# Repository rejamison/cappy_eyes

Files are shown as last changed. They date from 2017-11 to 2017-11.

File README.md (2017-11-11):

# cappy_eyes

Fun little project to create a moving pair of Cappy eyes for a hat.

Cappy Eyes

## 3D Printing

|Part|Count|Material|Print Time|Supports|
|---|---|---|---|---|
|[cappy_eyes.stl](cad/cappy_eyes.stl)|x1|40g|5 hours|No|
|[cappy_eyes_pupil.stl](cad/cappy_eyes_pupil.stl)|x2|2g|1 hour|No|
|[cappy_eyes_pupils_rail.stl](cad/cappy_eyes_pupils_rail.stl)|x1|1g|10 mins|No|
|[cappy_eyes_mount.stl](cad/cappy_eyes_mount.stl)|x1|2g|20 mins|Yes|
|**Total**| |**45g**|**6 hours**|

* Printed on Ultimaker 2 using Polymaker PolyMax PLA.
* 25% infill.

## Assembly

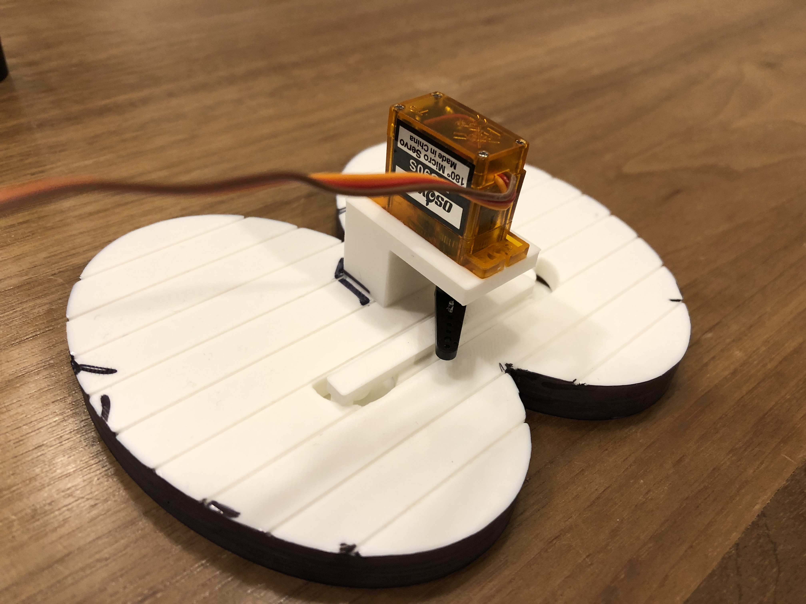
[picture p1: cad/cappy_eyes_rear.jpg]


1. If you plan to paint the parts, do so before assembly.
1. Place the pupils rail part into the half-circle holes in the eyes.  It should glide freely left and right in the half-circles.  If not, trim up the edges of the half-circles and/or sand the pegs on the rail.
1. Glue the pupils onto the pegs of the pupil rail, being careful not to accidentally glue the pupils to anything else.  You'll also want to be careful to ensure they're vertically straight or they'll rub on the side of the eyes.
1. Wiring:
   1. Connect the #0 data pin of the Trinket to the orange data wire of the Servo.
   1. Connect the USB+ pin of the Trinket to the red wire of the Servo.
   1. Connect the Gnd pin of the Trinket to the brown wire of the Servo.
   1. Plug the Trinket into your computer or the battery to power it up.
1. Program the Trinket (see [Software](#Software) below).
1. Once everything is working, screw in or glue the servo onto the mount.
1. Calibrate the servo arm:
   1. Place an arm onto the servo.  
   1. While the servo is unpowered, gently move the servo arm clockwise until it can't go any further.  
   1. Re-place the arm so that it's perpendicular to the servo pointing to the left.  
   1. Gently rotate the arm 180 degrees until it stops moving again.  
   1. Check that it's perpendicular in the other direction.  If it swings a little bit further (i.e., the servo has more than 180 degrees of travel), adjust the arm again so that the arm reaches the same angle on both ends of the servo's range.
1. Make a rigid metal pin that's small enough to move freely inside the servo arm.  I used a small paperclip.  Insert the pin into the center of the pupil rail by heating up one end and letting it melt into the rail.
1. Test-fit the mount and servo so that the pin fits into the servo arm and when you move the arm back and forth the rail moves smoothly.  Glue the mount onto the back of the eyes in that position.
1. Power it up and the pupils should move :)
1. Use a red and black Sharpie or paint spruce them up.

## Software

I used the Adafruit Trinket 5V.  Checkout their guide for how to setup the Arduino IDE to program the device:  https://learn.adafruit.com/introducing-trinket

The Trinket lacks PWM, so I used the Adafruit SoftServo library, but had to modify its parameters to get the OSOYOO MG90S servo to rotate it's full 180 degrees.  The modified library is included in `arduino/Adafruit_SoftServo`.  Load that library into your Arduino IDE for use in the sketch.

Program the trinket using the sketch:  `arduino/cappy_eyes.ino`.

The servo should move to a random position every few seconds.

## Bill of Materials

|Basic Tools & Materials|
|---|
|Soldering Iron and Solder|
|Wire Strippers|
|Wire|
|CA Glue|
|Short USB-A to Micro-USB Cable|
|Black and Red Sharpie or Paint|
|Heat-Shrink Wire Wrap and Heat Gun (Optional)|

|Item|Count|Unit Price|Total|Link|Notes|
|---|---|---|---|---|---|
|Adafruit Trinket 5V|1|$7|$7|[Adafruit](https://www.adafruit.com/product/1501)||
|Anker Powercore+ Battery|1|$14|$14|[Amazon](https://www.amazon.com/gp/product/B005X1Y7I2/ref=oh_aui_detailpage_o02_s01?ie=UTF8&psc=1)|Overkill for this project, but wanted to use a USB battery to simplify things.|
|Landisun Mario Cap|1|$12|$12|[Amazon](https://www.amazon.com/gp/product/B00NCRBEHG/ref=oh_aui_detailpage_o04_s00?ie=UTF8&psc=1)|Comes with Luigi too, but cheapest option even so.|
|OSOYOO MG90S Servo|1|$3|$3|[Amazon](https://www.amazon.com/OSOYOO-Helicopter-Airplane-Controls-Raspberry/dp/B073B5D5HD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)||
|**Total**| | |**$36**|||

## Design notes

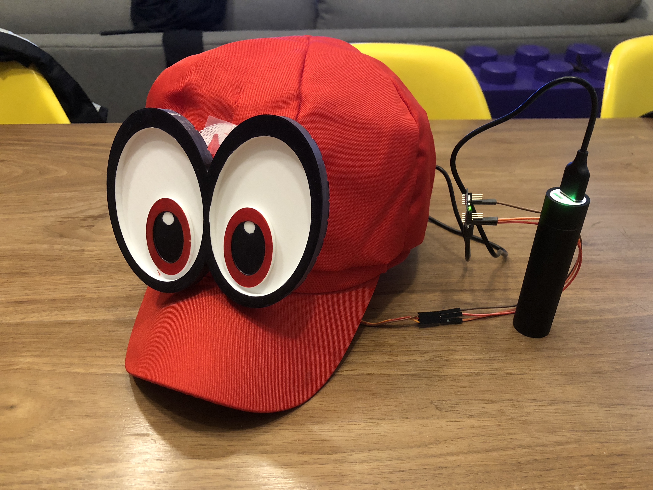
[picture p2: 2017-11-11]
cad/cappy_eyes_hero_static.jpg

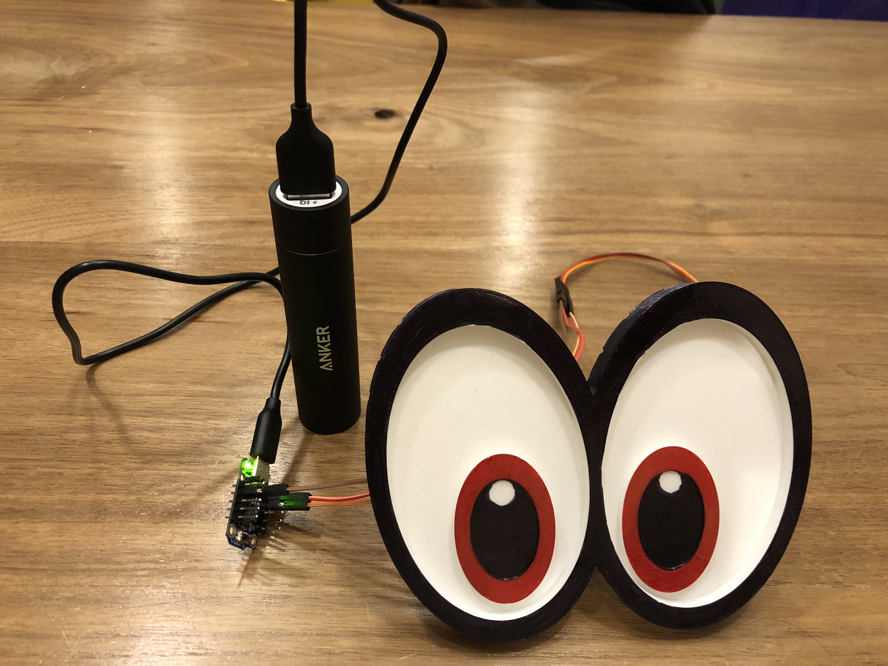
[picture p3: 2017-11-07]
cad/cappy_eyes_front.jpg

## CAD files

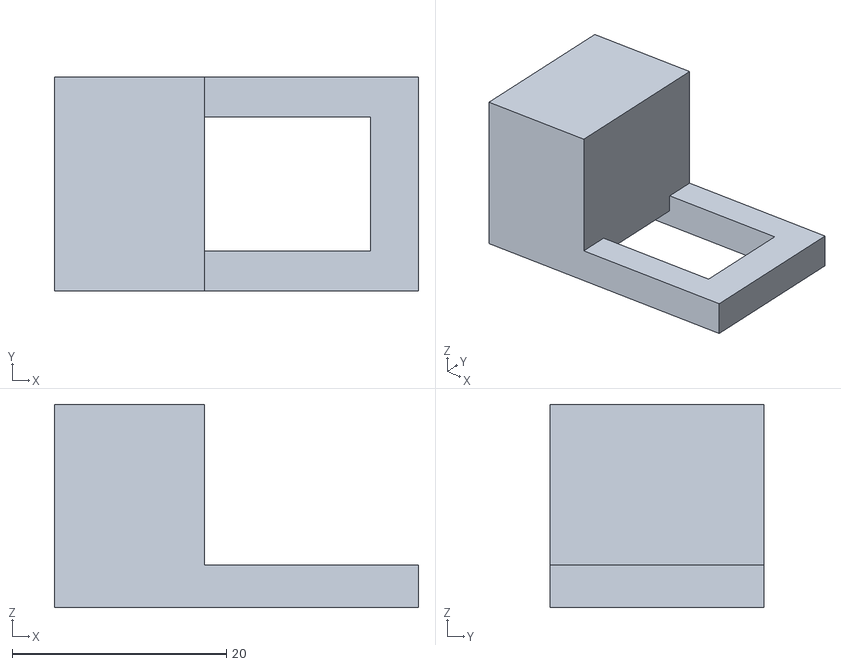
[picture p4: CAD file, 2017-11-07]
cad/cappy_eyes_mount.stl
34.0 x 20.0 x 19.0

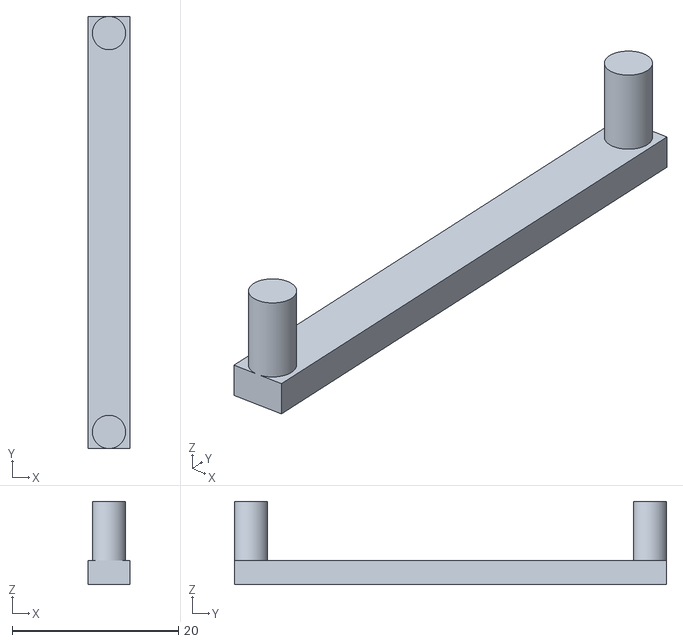
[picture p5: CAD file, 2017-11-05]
cad/cappy_eyes_pupils_rail.stl
5.00 x 52.0 x 10.0

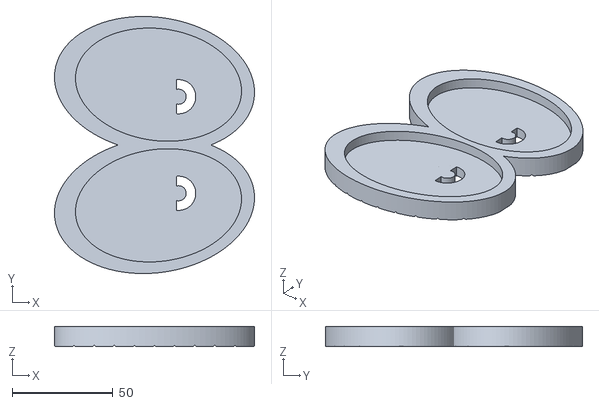
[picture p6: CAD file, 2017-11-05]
cad/cappy_eyes.stl
99.4 x 127.8 x 10.0

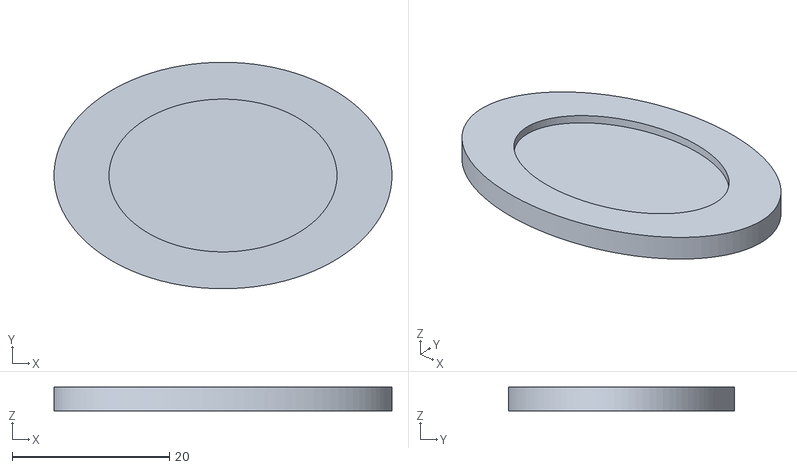
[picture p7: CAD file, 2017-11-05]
cad/cappy_eyes_pupil.stl
43.0 x 28.8 x 3.00

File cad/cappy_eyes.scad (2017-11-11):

$fn=100;

size = 1;

//translate([12*size - 5.5,0,-23.5]) mg90s();
translate([-7,0,0]) mount();

//eyes();
translate([12*size,6,0]) {
    //translate([0,0,6]) pupils();
    //pupils_rail();
}

//pupil();

module eyes() {
    difference() {
        union() {
            difference() {
                union() {
                    translate([0,-30*size,0]) rotate([0,0,8]) scale([1,.67,1]) cylinder(h=10,d=100*size);
                    translate([0,30*size,0]) rotate([0,0,-8]) scale([1,.67,1]) cylinder(h=10,d=100*size);
                }
                translate([2*size,-30*size,5]) rotate([0,0,8]) scale([1,.67,1]) cylinder(h=10,d=83*size);
                translate([2*size,30*size,5]) rotate([0,0,-8]) scale([1,.67,1]) cylinder(h=10,d=83*size);
                
                translate([12*size,-24*size,-1]) rotate([0,0,0]) cylinder(h=10,d=17);
                translate([12*size,24*size,-1]) rotate([0,0,0]) cylinder(h=10,d=17);
            }
            translate([12*size,-24*size,0]) rotate([0,0,0]) cylinder(h=4.99,d=7.5);
            translate([12*size,24*size,0]) rotate([0,0,0]) cylinder(h=4.99,d=7.5);
            translate([12*size-9,-(100*size)/2,0]) cube([8,100*size,4.99]);
        }
        groove_size = 1;
        for(i=[-100:10:100]) {
            translate([i,100,0]) rotate([90,0,0]) rotate([0,0,45]) translate([-groove_size/2,-groove_size/2,0]) cube([groove_size,groove_size,200]);
        }
    }
}

module pupil() {
    difference() {
        scale([1,.67,1]) cylinder(h=3,d=43*size);
        translate([0,0,2]) scale([1,.67,1]) cylinder(h=10,d=29*size);
        translate([0,0,-.01]) cylinder(h=1, d=4);
    }
}

module pupils() {
    translate([0,-24*size,0]) pupil();
    translate([0,24*size,0]) pupil();
}

module pupils_rail() {
    translate([0,-24*size,-3]) rotate([0,0,0]) cylinder(h=10,d=4);
    translate([0,24*size,-3]) rotate([0,0,0]) cylinder(h=10,d=4);
    
    translate([-2.5,-(52*size)/2,-3]) cube([5,52*size,2.9]);
}

module mount() {
    translate([-3,-10,-12]) cube([13,20,17]);
    translate([-4,-10,-14]) cube([6,20,19]);
    //translate([-0.55,0,-17]) cylinder(h=3,d=1.8);
    translate([-3,-10,-14]) cube([33,3.75,4]);
    translate([-3,10-3.75,-14]) cube([33,3.75,4]);
    translate([25.5,-10,-14]) cube([4.5,20,4]);
    //translate([27.55,0,-17]) cylinder(h=3,d=1.8);
}

module mg90s(){
	difference(){			
		union(){
			color("blue") cube([23,12.5,22], center=true);
			color("blue") translate([0,0,8.2]) cube([32,12.5,2.6], center=true);
			color("blue") translate([5.5,0,2.75]) cylinder(r=6, h=25.75, $fn=20, center=true);
			color("blue") translate([-.5,0,2.75]) cylinder(d=5.5, h=25.75, $fn=20, center=true);	
			color("white") translate([5.5,0,3.65]) cylinder(r=2.35, h=29.25, $fn=20, center=true);				
		}
		
		for ( hole = [14,-14] ){
			translate([hole,0,8.2]) cylinder(d=2, h=4, $fn=20, center=true);
            translate([hole,0,8.2]) cube(d=2, h=4);
		}	
        translate([14,-.5,3]) cube([10,1,10]);
        translate([-24,-.5,3]) cube([10,1,10]);
	}
}

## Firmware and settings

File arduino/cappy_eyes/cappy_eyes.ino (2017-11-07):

#include <Adafruit_SoftServo.h>  // SoftwareServo (works on non PWM pins)

#define SERVO1PIN 0   // Servo control line (orange) on Trinket Pin #0
Adafruit_SoftServo myServo1;
   
void setup() {
  // Set up the interrupt that will refresh the servo for us automagically
  OCR0A = 0xAF;            // any number is OK
  TIMSK |= _BV(OCIE0A);    // Turn on the compare interrupt (below!)

  randomSeed(analogRead(1));
  
  myServo1.attach(SERVO1PIN);
  myServo1.write(90);
  delay(15);
}

void loop()  {
  int servoPos = random(10, 170);
  int pause = random(1000);
  
  myServo1.write(servoPos);
  delay(2000 + pause);
}

// We'll take advantage of the built in millis() timer that goes off
// to keep track of time, and refresh the servo every 20 milliseconds
// The SIGNAL(TIMER0_COMPA_vect) function is the interrupt that will be
// Called by the microcontroller every 2 milliseconds
volatile uint8_t counter = 0;
SIGNAL(TIMER0_COMPA_vect) {
  // this gets called every 2 milliseconds
  counter += 2;
  // every 20 milliseconds, refresh the servos!
  if (counter >= 20) {
    counter = 0;
    myServo1.refresh();
  }
}

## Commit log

2017-11-05 First commit.
    [cappy_eyes.scad, cappy_eyes.stl, cappy_eyes_pupil.stl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]
2017-11-11 Initial commit.
    [cappy_eyes.scad]
